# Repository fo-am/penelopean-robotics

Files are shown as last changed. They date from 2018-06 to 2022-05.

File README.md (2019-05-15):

# Penelopean Robotics

Penelopean robots are modular, reconfigurable, dis-assemblable and
soft. They are part of the [Penelope Project](https://penelope.hypotheses.org/), a Study of Weaving as a
Technical Mode of Existence.

See a video of our [first swarm robotics maypole dancing test.](https://www.youtube.com/watch?v=NbzEvIek4nM)

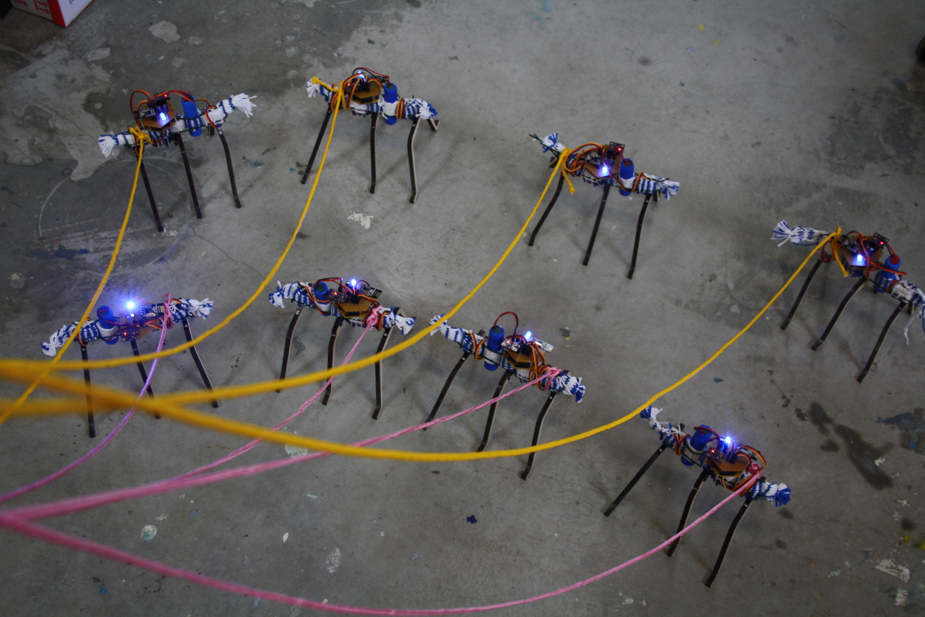
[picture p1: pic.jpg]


Penelopean robot swarms are designed for weaving ancient Greek looms
and maypole dancing. They can be livecoded remotely by a Raspberry Pi
and can be synced to musical beats for performances. Here is an
example of two maypole dances to create weaves we are currently
working on:

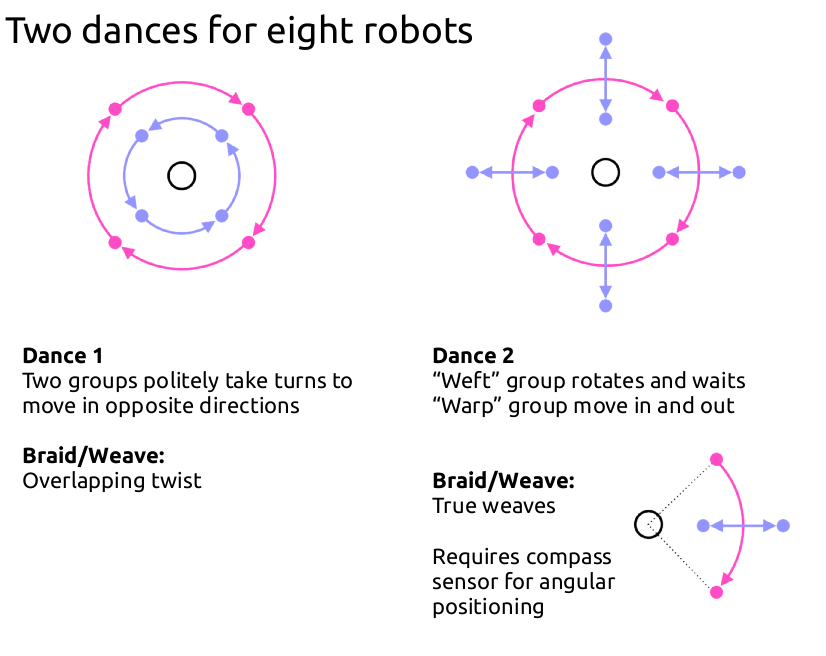
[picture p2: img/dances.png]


All source code and hardware files are here, each robot is made from:

* Tablet woven flexible structure holding everything together (see below)
* 3 SG92R microservos to drive the legs
* 1 3.7v li-ion battery
* Nrf24L01 radio module for remote control/programming
* GY91 accelerometer/gyro/compass sensor module
* Custom Atmega328 main pcb
* Radio, sensor and servo breakout secondary pcb
* 3 laser cut ply leg pairs

## Woven construction

Each robot is constructed using tablet weaving, an ancient human
technology dating back to neolithic times (and one of the few forms of
weaving that has never been mechanised).

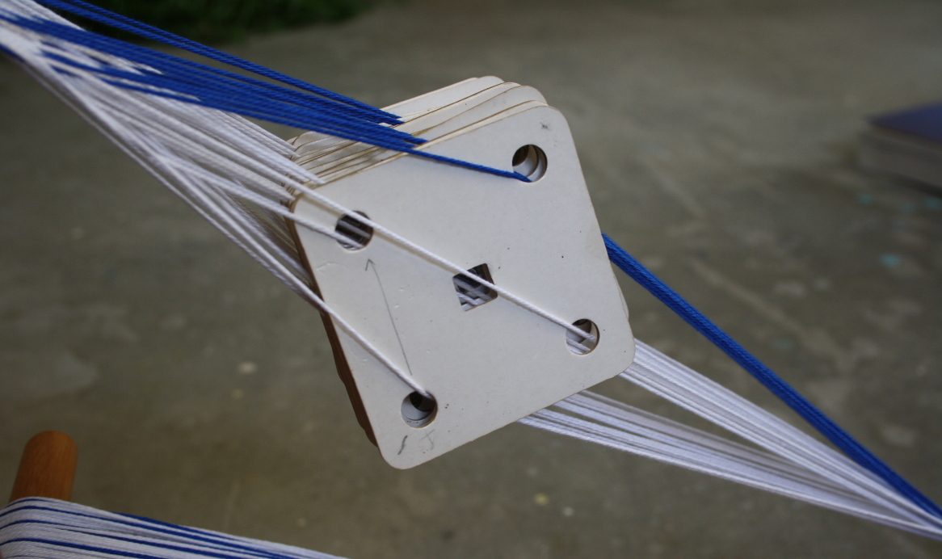
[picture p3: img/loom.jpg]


Tablet looms are simple to set up, and consist of a stack of cards
with holes punched in the corners through which the warp yarn passes.
[See here for a description of how to set up tablet loom](http://davesblog.fo.am/2016/02/how-to-warp-a-tablet-loom-neolithic-digital-computing-device/).

Usually tablet weaving produces a strong braid. For the penelopean
robotics we use a technique known as Icelandic double weave, where we
weave with the cards rotated at 45 degrees and use two wefts at the
same time. This converts the usually flat "2D" weave into a "3D"
structure, which we can use to support all the components for the
robot.

The exact spacing required will depend on the kind of yarn you are
using (I recommend 100% cotton or other plant based yarns - as wool is
too fluffy) but using this yarn I measured out 10 wefts to hold an
SG92R microservo and 8 for the 18mm diameter cylindrical battery.

Here is an attempt at notating the steps required in full. We start
with a supporting weave using normal single weft weaving, and then
start splitting to to hold the 3 servos and a battery, finishing with
an final supporting weave [todo: later version included a spacer to
make the legs equidistant]

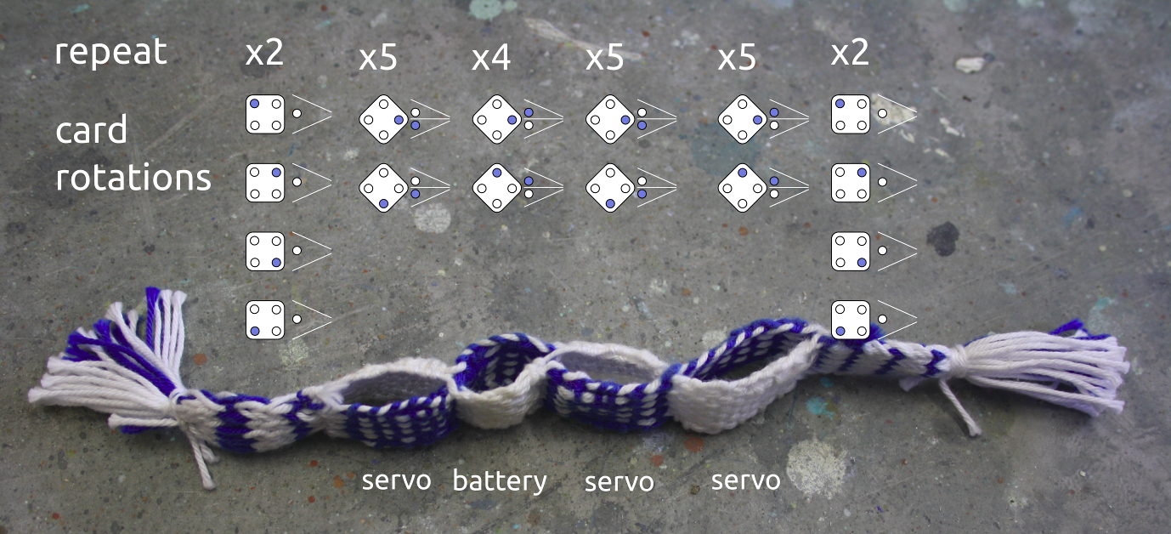
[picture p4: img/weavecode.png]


As the structure is woven into the fabric it is strong and able to
cope with the forces involved. The final stage is to stitch the
components into the structure to hold them in place along with some
thick wire to give the legs something to push against.

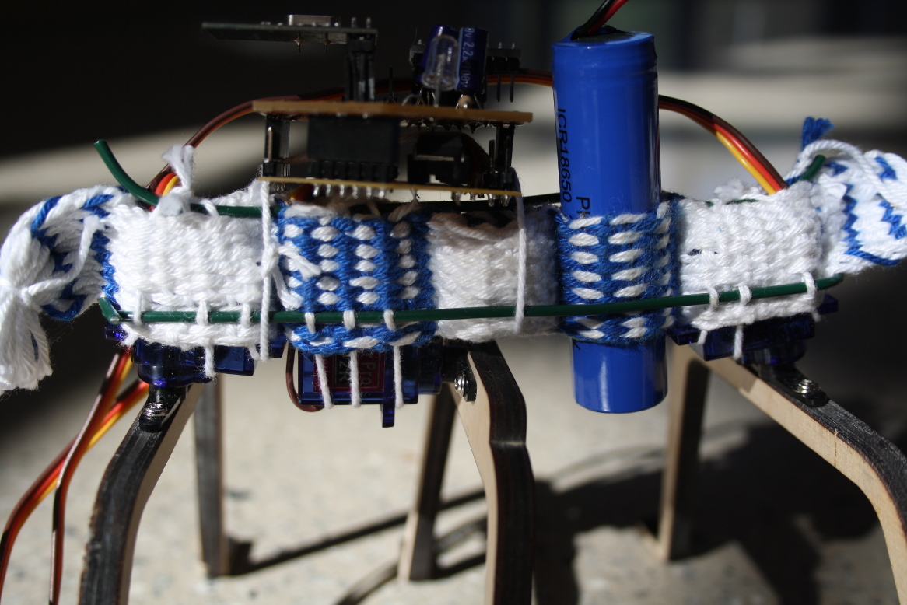
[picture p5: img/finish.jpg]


[todo: bioresin research]

## Raspberry Pi swarm controller setup

The swarm of robots is controlled by a Raspberry Pi running a python
program which is in charge of distributing commands to the robots. 

[under development]

## Movement sequencer

The robot servos are controlled via a "movement pattern sequencer"
which interprets symbols representing angles of rotation. This is
designed to allow different kinds of movement to be experimented with
as well as synchronisation with music, across the swarm.

By default a pattern consists of a 12 byte array, where each servo is
controlled by 4 symbols that are looped.

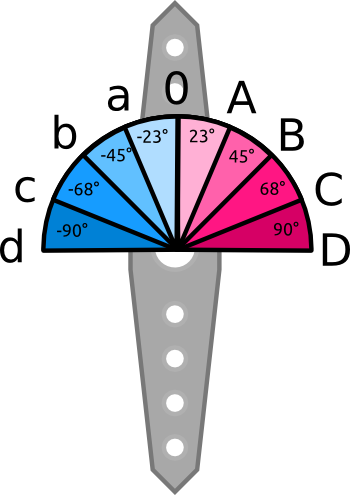
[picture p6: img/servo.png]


Various predefined patterns can be selected via bytecode programs (see
NEXT_PATTERN below) which correspond to:

    0000 0000 0000 : All stop - all servos to their central position.
    AAaa AaaA AAaa : Walk forward
    AAaa aAAa AAaa : Walk backwards

## The Yarn bytecode language

One of the problems with having numerous robots is updating and
distributing code changes to them. In order to make this process more
versatile we use a livecoding system where bytecode can be sent over
radio and written directly to memory. This bytecode is interpreted by
a machine running on the robot which can be halted and reset over
radio (separately to the main process, running the radio, controlling
servos and reading sensors etc, which continues as normal).

The robot bytecode (called yarn) has access to a set of registers that
describe the current state of the robot, including the movement
sequencer and sensor information. Registers can also be written to
that change the current servo motion pattern or light the LED for
example.

Writing the bytecode directly is considered a temporary inconvenience
before a compiler for a decent high level language is designed.

## Register description

| Name | Address | Read/Write | Description |
| --- | --- | --- | --- |
| ROBOT_ID | 0 | r | Identifier of this robot (same code as the last byte of the radio pipe address) |
| PC_MIRROR | 1 | r | A copy of the program counter for debugging. Writing to this has no effect. |
| LED | 2 | r/w | The state of the onboard blue LED. | 
| COMP_ANGLE | 3 | r | Current absolute compass angle from the magnetometer. |
| COMP_DELTA_RESET | 4 | w | Resets the relative compass angle calculation. |
| COMP_DELTA | 5 | r | Relative compass angle calculation, from last reset. |
| STEP_COUNT | 6 | r | How many times the current movement sequence has run (not really a step as each sequence has two steps). |
| STEP_COUNT_RESET | 7 | w | Resets the step counter register to zero. |
| NEXT_PATTERN  | 8 | r/w | Stores a pattern ID for use when the current motion sequence has finished. Can be one of NULL (Keep the last pattern), ALL_STOP (Cease all servo movement), WALK_FORWARDS: Move forward or WALK_BACKWARDS (Move backwards) |
| A | 9 | r/w | User defined register for convenience. A is currently used as the maypole dance status to synchronise multiple groups of robots. |
| B | 10 | r/w | User defined register for convenience. |
| C | 11 | r/w | User defined register for convenience. |
| D | 12 | r/w | User defined register for convenience. |
| SERVO_MS_PER_STEP | 13  | r/w | This controls the overall speed of the motion sequencer - in milliseconds per step. |
| SERVO_1_AMP | 14 | r/w | See below |
| SERVO_2_AMP | 15 | r/w | See below |
| SERVO_3_AMP | 16 | r/w | Separate control over the amplitude of each servos movement. Set these to zero will immediately prevent any movement while the sequencer still runs. This is a fixed point value where 1000 (the default) is equal to one, so setting to 2000 will double the amplitude and range of the servo. |
| SERVO_1_BIAS  | 17 | r/w | See below |
| SERVO_2_BIAS  | 18 | r/w | See below |
| SERVO_3_BIAS  | 19 | r/w | Sets the effective zero degrees position of each servo. This can be used either for fine tuning or in the case of the middle servo (2) can be used to steer the robot when walking. |
| SERVO_1_SMOOTH | 20 | r/w | See below |
| SERVO_2_SMOOTH | 21 | r/w | See below |
| SERVO_3_SMOOTH | 22 | r/w | To prevent sudden movements from breaking the robot or causing it to jump, each servo has a smoothing (low pass filter) applied in software to the desired rotation. This can be removed by setting this to zero, this is a fixed point number where 200 (0.2) is the default value. |
 
## Yarn instruction set

Yarn bytecode is a 16 bit stack based microcode language. 

### Program flow control instructions

| Bytecode instruction name | Example | Description |
| --- | ---| --- |
| nop | nop | No operation, do nothing for one cycle |
| jmp | jump label | Unconditional jump | 
| jpr | jpr  -2 | Unconditional jump relative (can be negative) |
| jpz | jpz  label | Jump only if the top of stack is zero. |
| jprz | jprz 10 | Jump relative if the top of the stack is zero. |

### Stack manipulation instructions

| Bytecode instruction name | Example | Description |
| --- | ---| --- |
| ldl | ldl  1207 | Load literal value on to stack |
| ld | ld STEP_COUNT | Load the contents of address on to the sta |
| ldi | ldi  A | Load indirect: the contents of the address pointed to by value (for arrays). | 
| st | st NEXT_PATTERN | Stores the top of the stack in the supplied address |
| sti | sti  A | Stores indirectly the stack top to the address at this location |
| dup | dup | Pushes the value at the top of the stack to duplicate it |  

### Number comparison instructions

| Bytecode instruction name | Example | Description |
| --- | ---| --- |
| lt | lt | Less than: Pushes 1 if the top of the stack is less than the stack item beneath it (pops both values) otherwise pushes 0 | 
| gt | gt | Greater than: Pushes 1 if the top of the stack is less than the stack item beneath it (pops both values) otherwise pushes 0 |
| lte | lte | Less than or equal: Pushes 1 if the top of the stack is less than or equal to the stack item beneath it (pops both values) otherwise pushes 0 | 
| gte | gte | Greater than or equal: Pushes 1 if the top of the stack is greater than or equal to the stack item beneath it (pops both values) otherwise pushes 0 | 
| slt | slt | Signed version of lt |
| sgt | sgt | Signed version of gt |
| slte | slte | Signed verion of lte |
| sgte | sgte | Signed verion of gte |

### Maths

| Bytecode instruction name | Example | Description |
| --- | ---| --- |
| add | add | Pops the top two stack items and pushes the sum of them | 
| sub | sub | Pops the top two stack items and pushes the top subtracted from the second |
| inc | inc | Adds one to the top of the stack |
| dec | dec | Subtracts one from the top of the stack |
| and | and | Bitwise ands the top two stack items |
| or | or | Bitwise ors the top two stack items |
| xor | xor | Bitwise xors the top two stack items |
| not | not | Bitwise nots the top stack item |
| rr | rr | Rotates the top stack item one bit to the right |
| rl | rl | Rotates the top stack item one bit to the left |
| sin | sin | Pushes the sine of the top stack item in degrees |
| cos | cos | Pushes the cosine of the top stack item in degrees |
| tan | tan | Pushes the tangent of the top stack item in degrees |
| rnd | rnd | Pushes and random number |
| inci | inci | Increments value in address in-place |
| deci | deci | Decrements value in address in-place |
| incp | incp | Increments value in address in-place and pushes it on the stack, convenience for looping |
| decp | decp | Decrements value in address in-place and pushes it on the stack, convenience for looping |

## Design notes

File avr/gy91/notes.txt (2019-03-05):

GY-91 sensor module
-------------------

i2c addr:0x68 MPU 6500 accelerometer/gyro

MPU-9150 magnetometer
to turn on:
(# set bypass mode for magnetometer
 self.bus.write_byte_data(self.addr, 0x37, 0x02))

i2c addr:0x0c AK8963 magnetometer

i2c addr:0x76 BMP280 digital pressure sensor

(d0 = 0x58 chip id)

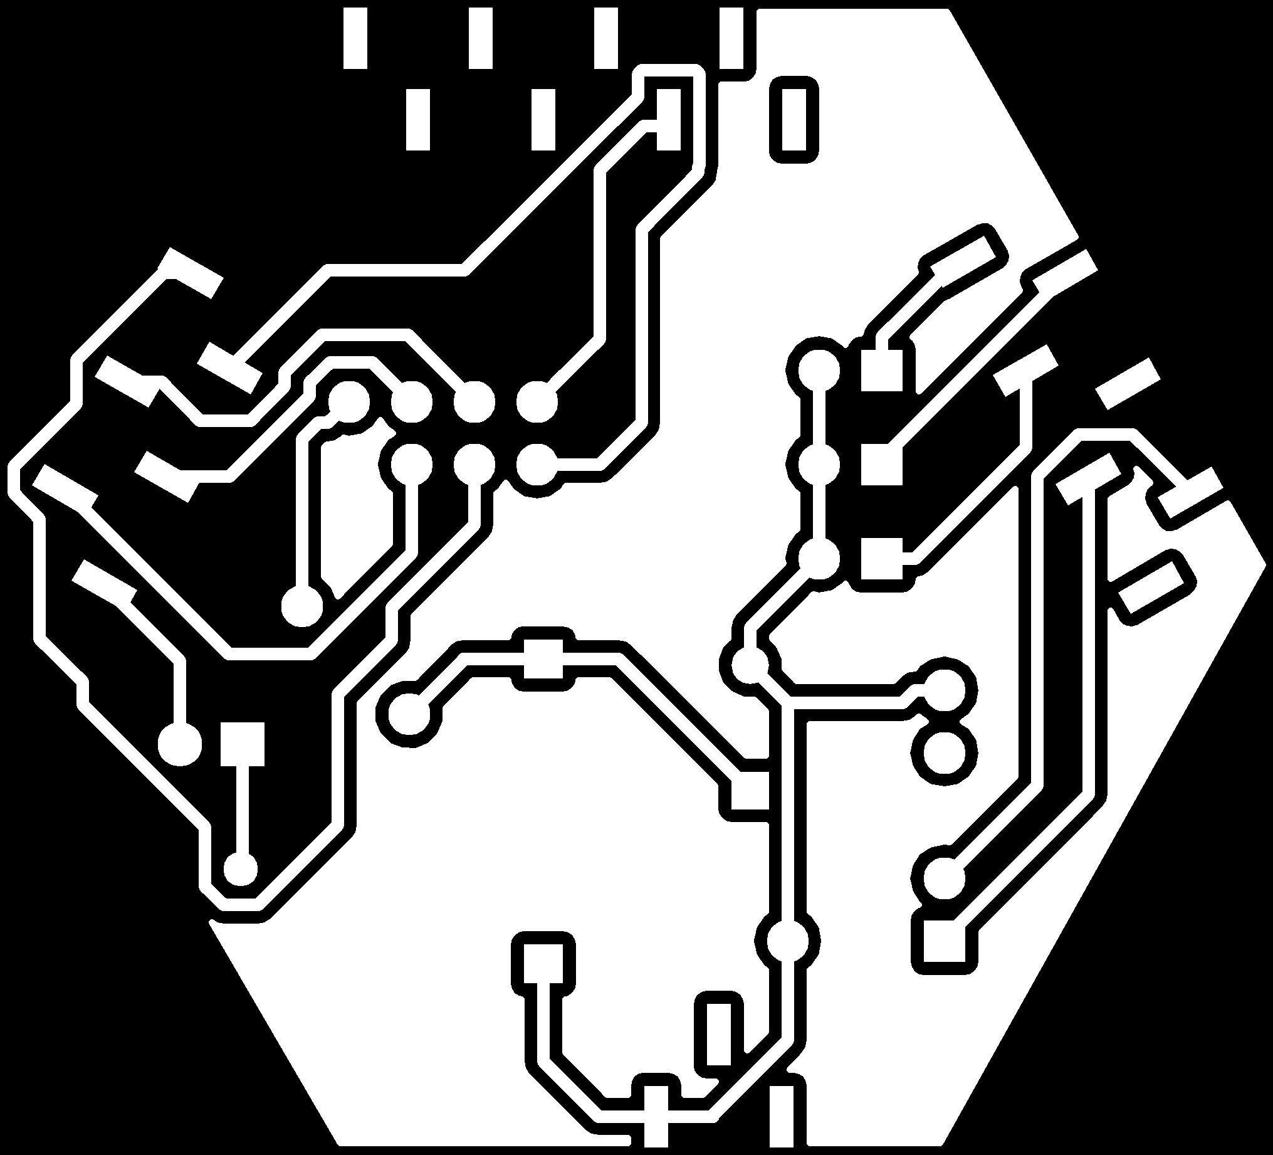
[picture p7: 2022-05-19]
pcb/robotv2/gerber/outp0_original_back.png

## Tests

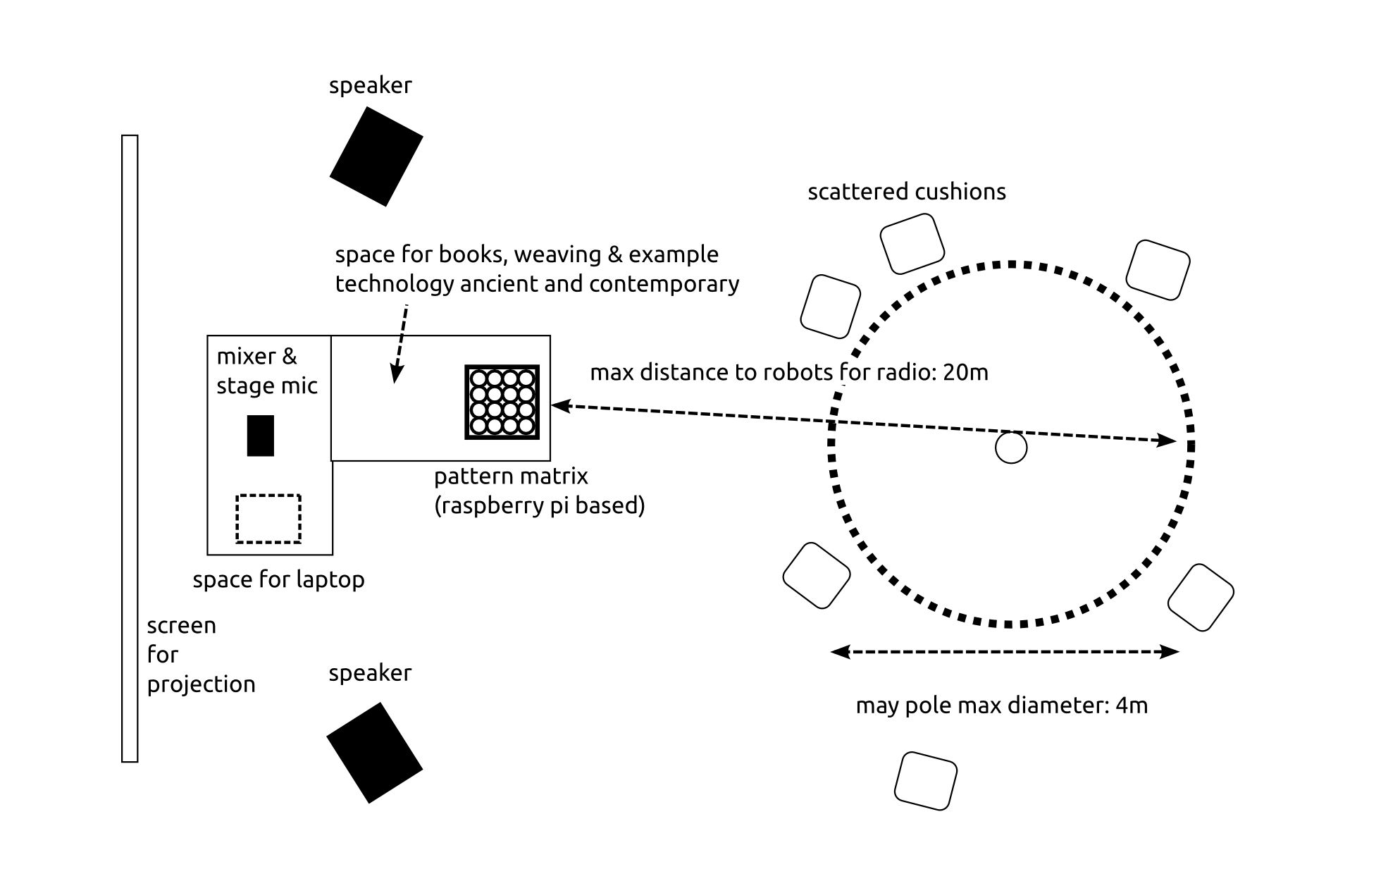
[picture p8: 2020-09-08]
performance/layout.png

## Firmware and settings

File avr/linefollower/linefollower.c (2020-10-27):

// Penelopean Robotics Copyright (C) 2020 FoAM Kernow
// 
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
#include <avr/io.h>
#include <avr/interrupt.h>
#include <util/delay_basic.h>
#include <util/delay.h>
#include "usiTwiSlave.h"
#include "camera.h"
#include "adc.h"
#include "pattern_recognition.h"

#define I2C_ADDR 0x0a
#define IMAGE_SIZE 128
#define FEATURES_SIZE 20

unsigned char image[IMAGE_SIZE];
feature features[FEATURES_SIZE];
unsigned int num_features=0;
unsigned char counter=0;

// change constants in yarnc.scm too
#define ADDR_ID 0
#define ADDR_I2C 1 
#define ADDR_ALIVE 2
#define ADDR_EXPOSURE_LO 3 // r/w
#define ADDR_EXPOSURE_HI 4 // r/w
#define ADDR_COURSENESS 5  // r/w
#define ADDR_MIN_WIDTH 6   // r/w
#define ADDR_MAX_WIDTH 7   // r/w
#define ADDR_AVERAGE 8
#define ADDR_LINE_MIDPOS 9
#define ADDR_BARCODE_BITS 10 // r/w
#define ADDR_BARCODE_SKIP 11 // r/w
#define ADDR_BARCODE_DATA 12  
#define ADDR_LINE_ERROR 13
#define ADDR_BARCODE_ERROR 14
#define ADDR_AUTOEXPOSURE 15 // r/w
#define ADDR_MODE 16 // r/w
#define ADDR_NUM_FEATURES 31
#define ADDR_FEATURES_START 32
#define ADDR_RAW_IMAGE_START 127

unsigned int  g_exposure=1000;
unsigned char g_courseness=10;
unsigned char g_min_width=20;
unsigned char g_max_width=255;
unsigned char g_average=0;
unsigned char g_line_midpos=0;
unsigned char g_barcode_bits=4;
unsigned char g_barcode_skip=1;
unsigned char g_barcode_data=0;
unsigned char g_line_error=0;
unsigned char g_barcode_error=0;
unsigned char g_autoexposure=100;
unsigned char g_mode=0;

uint8_t i2c_read(uint8_t reg) {
  switch (reg) {
  case ADDR_ID: return 0x1f; break; 
  case ADDR_I2C: return I2C_ADDR; break; 
  case ADDR_ALIVE: return counter++; break;
  case ADDR_EXPOSURE_LO: return g_exposure & 0xff; break;
  case ADDR_EXPOSURE_HI: return (g_exposure>>8) & 0xff; break;
  case ADDR_COURSENESS: return g_courseness; break;
  case ADDR_MIN_WIDTH: return g_min_width; break;
  case ADDR_MAX_WIDTH: return g_max_width; break;
  case ADDR_AVERAGE: return g_average; break;
  case ADDR_LINE_MIDPOS: return g_line_midpos; break;
  case ADDR_BARCODE_BITS: return g_barcode_bits; break;
  case ADDR_BARCODE_SKIP: return g_barcode_skip; break;
  case ADDR_BARCODE_DATA: return g_barcode_data; break;
  case ADDR_LINE_ERROR: return g_line_error; break;
  case ADDR_BARCODE_ERROR: return g_barcode_error; break;
  case ADDR_AUTOEXPOSURE: return g_autoexposure; break;
  case ADDR_MODE: return g_mode; break;
    // feature outputs
  case ADDR_NUM_FEATURES: return num_features; break;
  default:

    // output features
    if (reg>=ADDR_FEATURES_START && reg<3*FEATURES_SIZE) {
      unsigned int i = (reg-ADDR_FEATURES_START)/3;

      switch ((reg-ADDR_FEATURES_START)%3) {
      case 0: return features[i].start; break;
      case 1: return features[i].end; break;
      default: return features[i].width; break;
      }
    }    

    // raw image data is here...
    if (reg>=ADDR_RAW_IMAGE_START) {
      return image[reg-ADDR_RAW_IMAGE_START];
    }
    
    return 255;
  }
}

void i2c_write(uint8_t reg, uint8_t value) {
  switch (reg) {
  case ADDR_EXPOSURE_LO: g_exposure|=value; break;
  case ADDR_EXPOSURE_HI: g_exposure|=(int)(value)<<8; break;
  case ADDR_COURSENESS: g_courseness=value; break;
  case ADDR_MIN_WIDTH: g_min_width=value; break;
  case ADDR_MAX_WIDTH: g_max_width=value; break;
  case ADDR_BARCODE_BITS: g_barcode_bits=value; break;
  case ADDR_BARCODE_SKIP: g_barcode_skip=value; break;
  case ADDR_AUTOEXPOSURE: g_autoexposure=value; break;
  case ADDR_MODE: g_mode=value; break;
  }
}

///////////////////////////////////////////////////////////

int main() {
  DDRB = 0x00; // all inputs
  DDRB |= (1<<CLK_PIN); // output
  DDRB |= (1<<SI_PIN); // output
  init_adc();
  usiTwiSlaveInit(I2C_ADDR, i2c_read, i2c_write);
  sei();

  while (1) {
    read_camera(g_exposure,image);

    g_average = pattern_avg(image,IMAGE_SIZE);

    // alter exposure to centre avg
    if (g_autoexposure) {
      g_exposure=camera_autoexposure(g_exposure,g_average,g_autoexposure);
    }

    num_features=pattern_to_features(image,IMAGE_SIZE,
				     g_mode,
				     g_average,
				     g_courseness,
				     g_min_width,
				     g_max_width,
				     features,FEATURES_SIZE);
    
    g_line_error=pattern_read_line(features,FEATURES_SIZE,
				   &g_line_midpos);

    g_barcode_error=pattern_read_barcode(features,FEATURES_SIZE,
					 g_barcode_skip,
					 g_barcode_bits,
					 &g_barcode_data);    
  }
}

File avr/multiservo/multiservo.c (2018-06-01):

// up to 8 servos on portB sequentially pulsed
// uses timer1 in CTC mode
// synchro gap is constant, 6 ms
// frame is variable
// min.frame = 8*1+6 = 14 ms
// max.frame = 8*2+6 = 22 ms

// Mega88, 8 MHz
#define F_CPU 8000000UL

#include <avr/interrupt.h>
#include <avr/io.h>
#include <util/delay.h>

// initial pulse times in us for servo 0, 1, 2...7 (last value 6000 is the synchro gap)
unsigned int servo[9] = {1500, 1500, 1500, 1500, 1500, 1500, 1500, 1500, 6000};

//----------------------------------------------------------------

ISR(TIMER1_COMPA_vect)
{
  static unsigned char servo_num;
  PORTC = (1<<servo_num);          // end pulse for servo (n), start pulse for servo (n+1)            
  OCR1A = servo[servo_num];        // set width of pulse
  servo_num++;                     // prepare next servo 
  if(servo_num > 8) servo_num = 0; // again from servo 0;
}


int main (void)
{
      DDRC = 255;                        // portb output
      TCCR1B |= (1<<WGM12) | (1<<CS11);  // pwm mode 4,CTC, prescale=8
      TIMSK1 |= (1<<OCIE1A);             // enable T1_compareA interrupt 
      TCNT1 = 65530;
      sei();   

      uint32_t servo_min = 1000;
      uint32_t servo_max = 4500;
      uint32_t servo_mid = servo_min + ((servo_max-servo_min)/2);

      int32_t triangle_a = 0;
      uint8_t triangle_a_state = 0;
      int32_t triangle_b = 100;
      uint8_t triangle_b_state = 0;

      int32_t tri_max=200;
      int32_t tri_min=-200;

      int32_t mid_pos=-100;

      for(;;)                   
      {
	servo[0] = servo_mid+triangle_a;          // servos 0 and 1 left
	servo[1] = servo_mid+mid_pos;          // servos 0 and 1 left
	servo[2] = servo_mid+triangle_a;          // servos 0 and 1 left
	
	 
	 if (triangle_a_state) triangle_a-=4;
	 else triangle_a+=4;
	 if (triangle_a>tri_max) {
	   triangle_a_state=1;
	   mid_pos=400;
	 }
	 if (triangle_a<tri_min) {
	   triangle_a_state=0;
	   mid_pos=-400;
	 }

	 _delay_ms(20);
      }
}

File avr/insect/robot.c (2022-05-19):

// Penelopean Robotics Copyright (C) 2019 FoAM Kernow
// 
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
#include <avr/eeprom.h>
#include <avr/sleep.h>
#include <avr/wdt.h>
#include <gy91.h>
#include <servo.h>
#include <fixed.h>
#include <math.h>
#include <robot.h>
#include <avr/interrupt.h>
#include "i2c-master.h"
#include "adc.h"

// only have 1k of eeprom to play with...
// make sure it's init to zero with funky gcc stuff
// probably is zero anyway, but it makes the eep file so...
cell_t EEMEM ee_heap[HEAP_SIZE]={ [0 ... HEAP_SIZE-1] = 0 };

void robot_init(robot_t *r, unsigned char id) {
  yarn_init(&r->machine);
  robot_reset(r,id);
}

void robot_reset(robot_t *r, unsigned char id) {
  yarn_reset(&r->machine);
  r->running=1;
  r->id=id;
  // set up motion sequencer for default walk patterns
  servo_motion_seq_init(&r->seq, 4);
  // 500 ms = 120 bpm
  r->seq.ms_per_step=500;

  // non-zero defaults
  yarn_poke(&r->machine,REG_SERVO_MS_PER_STEP,500); 
  yarn_poke(&r->machine,REG_SERVO_1_AMP,MAKE_FIXED(1.0));
  yarn_poke(&r->machine,REG_SERVO_2_AMP,MAKE_FIXED(1.0));
  yarn_poke(&r->machine,REG_SERVO_3_AMP,MAKE_FIXED(1.0));
  yarn_poke(&r->machine,REG_SERVO_1_SMOOTH,MAKE_FIXED(0.2));
  yarn_poke(&r->machine,REG_SERVO_2_SMOOTH,MAKE_FIXED(0.2));
  yarn_poke(&r->machine,REG_SERVO_3_SMOOTH,MAKE_FIXED(0.2));
}

void robot_halt(robot_t *r) {
  r->running=0;
}

void robot_tick(unsigned int delta_ms, robot_t *r) {
  if (r->running) {
    yarn_machine *m = &r->machine;

    // update registers
    // for debugging, but pc should prob be an internal register anyway
    yarn_poke(m,REG_ROBOT_ID,r->id);
    //robot_update_sensors(r);
    robot_update_servos(r);
    yarn_run(m);
    // our ONE led - getting a bit tiresome
    if (yarn_peek(m,REG_LED)!=0) {
      PORTB |= 0x01;
    } else {
      PORTB &= ~0x01;
    }
    servo_motion_seq_update(delta_ms,&r->seq);

    if (yarn_peek(m,REG_SLEEP)==1) {
      yarn_poke(m,REG_SLEEP,0);
      robot_sleep();
    }

    // direct access to all i2c devices attached
    if (yarn_peek(m,REG_I2C_CTRL)!=0) {
      if (yarn_peek(m,REG_I2C_CTRL)==0x01) { // read
	unsigned char d=0;
	i2c_read_reg(yarn_peek(m,REG_I2C_DEVICE),yarn_peek(m,REG_I2C_ADDR),&d,1);
	yarn_poke(m,REG_I2C_DATA,d);
      }
      if (yarn_peek(m,REG_I2C_CTRL)==0x02) { // write
	unsigned char d=yarn_peek(m,REG_I2C_DATA);
	i2c_write_reg(yarn_peek(m,REG_I2C_DEVICE),yarn_peek(m,REG_I2C_ADDR),&d,1);		
      }
      yarn_poke(m,REG_I2C_CTRL,0);
    }	

    // not sure if adc is init or will mess with servos
    //yarn_poke(m,REG_VCC,(short)(internal_vcc(3)*100.0f));
  }
}

void robot_write_ee_heap(robot_t *r) {
  for (int n=0; n<HEAP_SIZE; n++) {
    eeprom_update_word((uint16_t*)(&ee_heap[n]),r->machine.m_heap[n]);
  }
}

void robot_read_ee_heap(robot_t *r) {
  for (int n=0; n<HEAP_SIZE; n++) {
    r->machine.m_heap[n]=eeprom_read_word((uint16_t*)(&ee_heap[n]));
  }
}

float angle_compare(float a1, float a2) {
  return 180 - fabs(fabs(a1 - a2) - 180);
}

void robot_update_sensors(robot_t *r) {
  yarn_machine *m = &r->machine;
  float x,y,z;
  gy91_read_accel(&x,&y,&z);
  yarn_poke(m,REG_ACCEL_X,MAKE_FIXED(x));
  yarn_poke(m,REG_ACCEL_Y,MAKE_FIXED(y));
  yarn_poke(m,REG_ACCEL_Z,MAKE_FIXED(z));
  gy91_read_gyro(&x,&y,&z);
  yarn_poke(m,REG_GYRO_X,MAKE_FIXED(x));
  yarn_poke(m,REG_GYRO_Y,MAKE_FIXED(y));
  yarn_poke(m,REG_GYRO_Z,MAKE_FIXED(z));
  gy91_read_mag(&x,&y,&z);
  yarn_poke(m,REG_COMP_X,MAKE_FIXED(x/100.0f));
  yarn_poke(m,REG_COMP_Y,MAKE_FIXED(y/100.0f));
  yarn_poke(m,REG_COMP_Z,MAKE_FIXED(z/100.0f));
  float angle=180+atan2(y,x)*57.2958;
  //angle+=180; // set range to 0-360
  yarn_poke(m,REG_COMP_ANGLE,(short)angle);
  // check and clear flag
  static float compare_angle=0;
  if (yarn_peek(m,REG_COMP_DELTA_RESET)==1) {
    yarn_poke(m,REG_COMP_DELTA_RESET,0);
    compare_angle=angle;
  }
  yarn_poke(m,REG_COMP_DELTA,(short)angle_compare(compare_angle,angle));
  yarn_poke(m,REG_TEMPERATURE,(short)(gy91_read_temp()*100.0f));
}

void robot_update_servos(robot_t *r) {
  yarn_machine *m = &r->machine;
  servo_motion_seq *seq = &r->seq;
  
  seq->ms_per_step = yarn_peek(m,REG_SERVO_MS_PER_STEP);

  // update servo movements
  seq->servo[0].amplitude = yarn_peek(m,REG_SERVO_1_AMP);
  seq->servo[0].bias_degrees = yarn_peek(m,REG_SERVO_1_BIAS);
  seq->servo[0].smooth = yarn_peek(m,REG_SERVO_1_SMOOTH);
  seq->servo[1].amplitude = yarn_peek(m,REG_SERVO_2_AMP);
  seq->servo[1].bias_degrees = yarn_peek(m,REG_SERVO_2_BIAS);
  seq->servo[1].smooth = yarn_peek(m,REG_SERVO_2_SMOOTH);
  seq->servo[2].amplitude = yarn_peek(m,REG_SERVO_3_AMP);
  seq->servo[2].bias_degrees = yarn_peek(m,REG_SERVO_3_BIAS);
  seq->servo[2].smooth = yarn_peek(m,REG_SERVO_3_SMOOTH);

  seq->next_pattern_id = yarn_peek(m,REG_SERVO_NEXT_PATTERN_ID);
  //seq->next_pattern_id = MOTION_SEQ_PATTERN_ID_FORWARD;

  if (yarn_peek(m,REG_SERVO_STEP_COUNT_RESET)==1) {
    yarn_poke(m,REG_SERVO_STEP_COUNT_RESET,0);
    seq->pattern_loop_count=0;
  }
  yarn_poke(m,REG_SERVO_STEP_COUNT,seq->pattern_loop_count);

}

// watchdog interrupt
/*ISR (WDT_vect) {
  wdt_disable(); // disable watchdog
  }*/
 
void robot_sleep() {
  // disable ADC
  ADCSRA = 0;
  // clear various "reset" flags
  MCUSR = 0;
  // allow changes, disable reset
  WDTCSR = _BV(WDCE) | _BV(WDE);
  // set interrupt mode and an interval
  WDTCSR = _BV(WDIE) | _BV(WDP3) | _BV(WDP0); // set WDIE, and 8 seconds delay
  wdt_reset(); // reset the watchdog
  set_sleep_mode (SLEEP_MODE_PWR_DOWN);
  cli(); // timed sequence follows
  sleep_enable();
  // turn off brown‐out enable in software
  MCUCR = _BV(BODS) | _BV(BODSE);
  MCUCR = _BV(BODS);
  sei(); // guarantees next instruction executed
  sleep_cpu ();
  // cancel sleep as a precaution
  sleep_disable();
  //adc_init();
}

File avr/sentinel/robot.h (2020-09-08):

// Penelopean Robotics Copyright (C) 2019 FoAM Kernow
// 
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
#include <yarn.h>
#include <gy91.h>
#include <servo.h>

#ifndef PENELOPE_ROBOT
#define PENELOPE_ROBOT

// memory map (exposed via telemetry)
// change yarnemu.py + yarnc.scm compiler registers too

#define REG_ROBOT_ID 2
#define REG_LED 3
#define REG_COMP_ANGLE 4
#define REG_COMP_DELTA_RESET 5
#define REG_COMP_DELTA 6
#define REG_SERVO_STEP_COUNT 7
#define REG_SERVO_STEP_COUNT_RESET 8
#define REG_SERVO_NEXT_PATTERN_ID 9
// telemetry visible user area
#define REG_USR_A 10
#define REG_USR_B 11
#define REG_USR_C 12
#define REG_USR_D 13

#define REG_TEMPERATURE 14 
#define REG_SLEEP 15       
#define REG_I2C_DEVICE 16
#define REG_I2C_ADDR 17
#define REG_I2C_DATA 18
#define REG_I2C_CTRL 19
#define REG_ADC_1 20
#define REG_ADC_2 21
#define REG_ADC_3 22
#define REG_VCC 23

#define REG_SERVO_MS_PER_STEP 14 // <- temperature 
#define REG_SERVO_1_AMP 15       
#define REG_SERVO_2_AMP 16
#define REG_SERVO_3_AMP 17
#define REG_SERVO_1_BIAS 18
#define REG_SERVO_2_BIAS 19
#define REG_SERVO_3_BIAS 20
#define REG_SERVO_1_SMOOTH 21
#define REG_SERVO_2_SMOOTH 22
#define REG_SERVO_3_SMOOTH 23

// 24->32 user area (enough RAM for anybody!!)

typedef struct {
  unsigned char id;
  unsigned char running;
  yarn_machine machine;
  servo_motion_seq seq;
  unsigned int last_move_type;
  unsigned int last_seq_pos;
} robot_t;

void robot_init(robot_t *r, unsigned char id);
void robot_reset(robot_t *r, unsigned char id);
void robot_halt(robot_t *r);
void robot_tick(unsigned int delta_ms, robot_t *r);
void robot_update_sensors(robot_t *r);
void robot_update_servos(robot_t *r);
void robot_write_ee_heap(robot_t *r);
void robot_read_ee_heap(robot_t *r);
void robot_sleep();

#endif

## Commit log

2018-01-15 id tests, problem with after error state needs hard nrf reset
    [radio.py, robot.py, swarm.py]
2018-01-16 removed urequired radio reset
    [app.py, radio.py, robot.py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]
2018-06-01 servo and radio work together
2018-06-06 fixed servos and smoothing
    [insect.c]
2018-10-03 syncing and single message for all servos
2019-03-05 started looking at sensors
2019-03-06 gy91 sensors working and tested, for when they are ready, and other fogotten directories...
    [proto.kicad_pcb, proto.sch, protomicro.kicad_pcb]
2019-03-25 new amp/bias and smooth and started breaking features out into register access for livecoding
    [proto-B.Adhes.gbr, proto-B.CrtYd.gbr, proto-B.Cu.gbr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]
2019-04-15 sensors working and stuff
    [proto.kicad_pcb, proto.sch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]
2019-04-18 magnetometer working etc
2019-04-23 servos work again
2019-04-26 compiler fixes and register tweaks
    [app.py, robot.c, robot.py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]
2019-05-09 default servo mid pos, stored program and stuff
2019-05-15 nrf fix and new pic
    [lib_nrf24.py]
2019-09-09 fixes for new sync registers and added pattern matrix stuff
    [pm.py, radio.py, robot.py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]
2019-09-21 fixed setting function arguments
    [main.c]
2019-09-25 finally eeprom and mag sensor working - I think
2019-10-15 sensor calibration and eeprom pi side stuff
2019-10-15 heap fix, and loads more movement patterns
    [insect.c, robot.c]
2019-10-17 turning by magnetometer works!
2020-08-27 added sleep, linefollower etc
    [linefollower.kicad_pcb, linefollower.sch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]
2020-08-28 camera and pattern recognition timing fixes and synthetic tests
    [camera.c, linefollower.c]
2020-08-29 linefollower fixes, integrating with insect/robot
    [adc.c, camera.c, insect.c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]
2020-09-08 turned off sensors to test camera
2020-09-08 compiler rotate fix and wacky regs
    [radio.py, yarnasm.py]
2020-11-12 yarncode runs and some error reporting
    [lib_nrf24.py, radio.py, robot.py]
2021-01-20 compiler + language fixes
    [yarnasm.py]
2022-05-19 added v2 pcb
    [proto-2022-01-21-09-49-23.sch, proto-2022-01-21-10-01-41.sch, proto-2022-01-21-10-04-52.sch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]

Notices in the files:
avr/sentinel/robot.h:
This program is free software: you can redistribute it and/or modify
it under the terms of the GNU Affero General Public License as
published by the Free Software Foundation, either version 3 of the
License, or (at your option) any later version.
